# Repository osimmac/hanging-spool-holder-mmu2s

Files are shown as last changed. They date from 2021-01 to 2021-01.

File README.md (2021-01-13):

# hanging-spool-holder-mmu2s
OpenSCAD design of a hanging spool holder, designed with simplicity, low friction, and reusing parts from MMU2S kit in mind.

--Features
 - Minimalist strong design, no supports needed, simple geometry
 - Reuses MMU2S Spool holder hardware, create up to 10 hanging spool holders!
 - High tech Self Stablizing roller, see this video for an explanation of how it works! (it was also the inspiration for the roller design) https://www.youtube.com/watch?v=Ku8BOBwD4hc
 - low rolling resistance, perfect for flexible filaments in the MMU2S! (ive had success printing 85A hardness filaments!)

--Required Hardware
- 1x Rod that came with MMU2S trays
- 2x Bearings that came with MMU2S trays 
- 2-4x Zipties that came with printer or MMU2S
- 0.8mm nozzle recommended

--How to get started if new to OpenSCAD
1. Download and install from here (os specific instructions are there): https://www.openscad.org/downloads.html
2. launch openscad and start messing around with the examples, they can be accessed from the launcher or "file" at the top of the application.  most of what i learned is from there. the examples are easy to modify and expand upon.
3. Check out the Basics > CSG-Modules.scad example, this spool holder uses modules. (though it could use them better)
3. Useful cheatsheet once you understand how the commands work: https://www.openscad.org/cheatsheet/index.html

--How to get started if not new to OpenSCAD :)
1. download and open spoolholder.scad from this repository
2. there are many comments within the file that explain whats going on; generally you will need to edit the variables near the top
3. comment out a few lines in the RENDERING /OUTPUT section, start with leaving test piece uncommented if you need to adjust fitment
4. Render (F6)
5. if it looks good, Export to STL (F7)!

--How to Print
(print test piece first)

Highly Recommend nozzle larger than 0.4mm, especially if using MMU2S. Less layer changes, less filiament swaps, smaller purge blocks with thicker layer heights, Faster Prints. they are cheap and worth it. This spool holder can be printed in under 3 hours while still making a strong print. I dont have settings for anything other than 0.8mm, you are welcome to try and post results as an issue or something.

(*used prusa slicer*)
  
  - PETG filament thats strong and reliable (you dont want 1kg mass falling on your printer)
  - Bed temp 70c, add gluestick, first layer temp 255c, other layers 265c
  - I had my petg set to 12mm^3/s max volumetric speed, its near the limit but allows for fast strong prints. its also why temp is so high.
  - I used a 0.6mm profile as a starting point and scaled all the settings for 0.8mm nozzle.
  - 0.8mm nozzle, recommend tuning extrusion multiplier, mine is set to 1.08
  - retraction for 0.8mm nozzle was set to 0.4mm
  - Extrusion width for 1st layer is 150%
  - all other extrusion width settings set to 0.9mm
  - 0.6mm layer height
  - 3 perimeters
  - 2 top and bottom layers
  - Rectiliear infill, 10% density on the interior
  - fast print speed settings, first layer speed set to 10mm/s
  - no support
  - make sure first layer sticks well
  - min 30% fan max 70%, disabled for first 2 layers, slow down if print speed is below 8 seconds per layer
        -slow down at most 4mm/s for cooling

--How to assemble
1. First print test piece with settings above
2. Clean out the hole with a razer or something, be careful not to enlarge the hole too much or break the blade. 
3. Get a rod and try push fitting it into the hole, it will require a lot of force
4. Try using a hammer, with plastic part facing down and rod pushing into carpet or something. dont bang the rod and dont do it on tile as the force may break it. gently but firmly hammer the test piece onto the rob. it should go in about 1cm. a full inserted rod will stick out about 10.8cm from the piece. its OK if a bit more sticks out if it feels secured. ideally 9mm or more will enter the part.. 
5. If it doesnt fit properly, try altering the test piece with openscad and generate an updated STL.
6. Repeat steps above until you get a good fitting rod that can hold 1kg without bending a bunch. 
7. Generate a new main arm if you altered the hole size.
8. Print everything
9. Trim parts
10. Press fit bearings into roller, be careful not to break it
11. Press fit rod into main arm, use hammer on plasic piece with rod in carpet.
12. Slide roller on, verify it rolls smoothly
13. press fit cap on, may need to trim peg
14. hang with zipties!

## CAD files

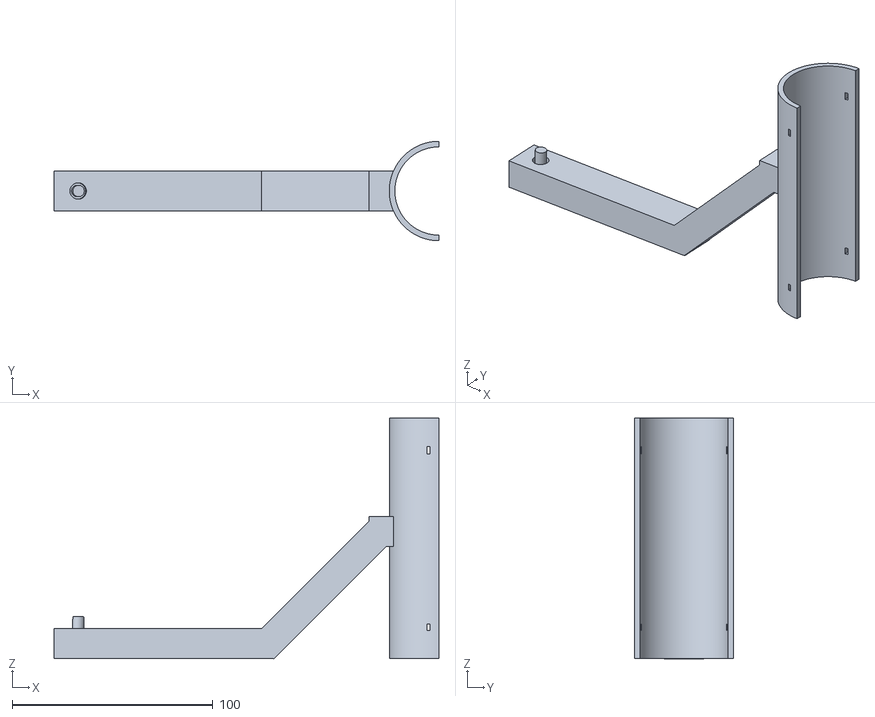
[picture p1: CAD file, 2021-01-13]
spoolholderfinal.stl
192.0 x 49.6 x 120.1

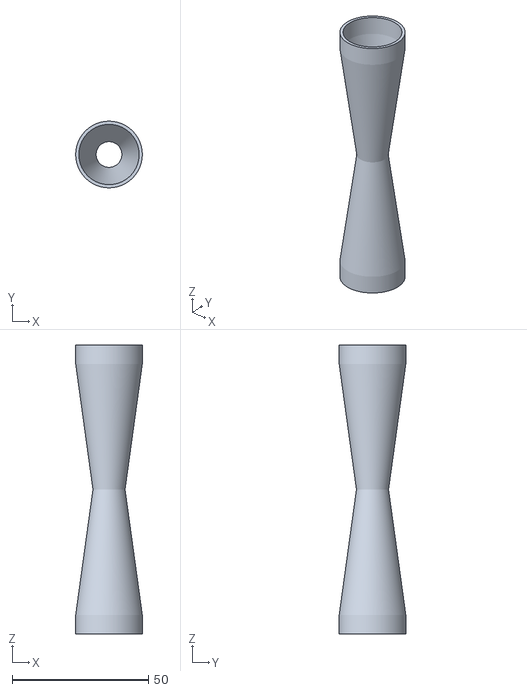
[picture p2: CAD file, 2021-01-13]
spoolrollerfinal.stl
24.4 x 24.4 x 106.0

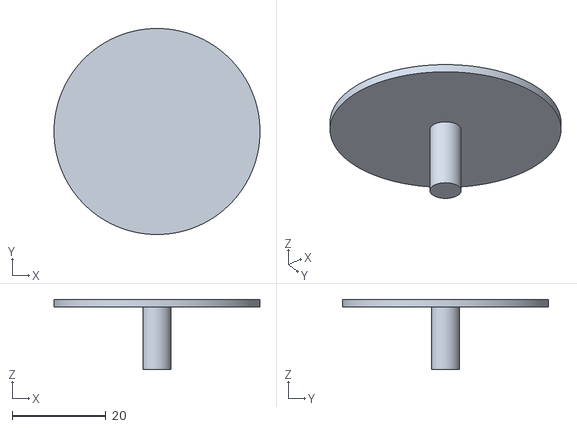
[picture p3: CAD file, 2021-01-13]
spoolcap.stl
44.0 x 44.0 x 15.0

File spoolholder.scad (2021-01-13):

  //  This program is free software: you can redistribute it and/or modify
  //  it under the terms of the GNU General Public License as published by
 ///   the Free Software Foundation, either version 3 of the License, or
 //   (at your option) any later version.
//
 //   This program is distributed in the hope that it will be useful,
  //  but WITHOUT ANY WARRANTY; without even the implied warranty of
  //  MERCHANTABILITY or FITNESS FOR A PARTICULAR PURPOSE.  See the
 //   GNU General Public License for more details.

 //   You should have received a copy of the GNU General Public License
 //   along with this program.  If not, see <https://www.gnu.org/licenses/>.

//FILAMENT SPOOL HOLDER DESIGNED FOR USE WITH MMU2S HARDWARE
//Designed by osimmac


//Dont mess with these variables
// Global resolution
$fs = 0.01;  // Don't generate smaller facets than 0.01 mm
$fa = 1;    // Don't generate larger angles than 5 degrees



//CONSTANTS FOR REFERENCE!
//bearing diameter = 22mm
//rod diameter = 7.85mm
//rod hole diameter = 6mm


//User Variables
//MAIN ARM VARIABLES
//Rod Hole size
  //changing the value below will change the size of the hole the rod is inserted to. try changing the size in 0.05 or 0.1mm increments. 
 holediameter = 8.2;
 
 //Rod peg size
  //changes size of peg that goes into rod
  pegdiameter = 5.7;
  
  
  //ROLLER VARIABLES
 //changes hole diameter for bearing
bearingdiameter = 22.08;


  //CAP VARIABLES
   //changes size of peg that goes into other end of rod, should be more snug than rodpegsize
  cappegdiameter = 5.75;


//RENDERING / OUTPUT BEGIN
//Leave only 1 uncommented to render and get STL for that object only. alter and print just the test piece if you need to adjust fitment for rod. If you just edit the fitment for the hole, then you can use orignal cap and roller stl and just render a new Main Arm. if not, do this  for each of the 3 pieces. spollroller(); should stay commented as its depricated.
//spoolroller();

//Test  Piece!!
translate([-50,0,0])testpiece();

//Roller Piece
 spoolroller2();
 
 //Cap Piece
rotate(180,[0,1,0])translate([0,0,-108])spoolcap();
 //Main Arm Piece
translate([0,0,-2])spoolarm();

//once setup, press f6 to render and then f7 to export as stl. these actions are also at the top of application. may need to add .stl to end of file when exporting.

//RENDERING /OUTPUT END!!!




//BEGINNGING OF ACTUAL CODE
//This spool holder is spilt up into modules/parts, these parts are:
//---Test Piece (for testing fitment)
//---Spool Roller 2 (it has the angled center)
//---Spool Rolled (depricated and lame)
//---Spool Cap (cap on the end)
//---Spool Arm (main structure)

//Test piece to test fitment of rod.
//Should be hard to insert but not impossible, it should go in around 1cm and feel secure
//NOTE: there is a 1.7 degree tilt in the hole to counter act sag when loaded with filament
module testpiece(){

    union(){
       
    rotate(1.7,[0,1,0])translate([0,0,-13])color("DarkGreen")cylinder(h=20,r=pegdiameter/2);
    difference(){
    translate([-12,-10,-14])color("Green")cube([25,20,15]);
     //changing the radius (r) of the cyclinder below will change the size of the hole the rod is inserted to. try changing the size in .05 or .1mm increments. 
    rotate(1.7,[0,1,0])translate([0,0,-11.8])cylinder(h=13,r=holediameter/2);
    }
    }

  
   }

//high tech self stablizing roller 
 //this is created by making a long thin polygon with 3 bends in it, requiring 10 points, translating it away from the origin by the radius of bearing and rotate extruding it around the z axis.
   
   //polygons start at the origin and work their way from there. its basically 2 lines with 5 points, offset with thickness of walls desired.
module spoolroller2(){

     color("Purple")rotate_extrude(angle=360) {
         translate([bearingdiameter/2,0,0])rotate([0,0,0])polygon([[0,0],[0,7.05],[-6.325,106/2],[0,106-7.05],[0,106],[1.175,106],[1.175,106-7.05],[-5.15,106/2],[1.175,7.05],[1.175,0]]);
     }
}

//deprecated flat roller
module spoolroller(){
    difference(){
    color("Blue")cylinder(h=106,r=bearingdiameter+2.4/2);
    translate([0,0,-.05])color("Red")
                            cylinder (h=106.1,r = bearingdiameter/2);
}
}   


//cap that goes on other end of rod and acts as safeguard preventing spool from coming off
module spoolcap(){
    union(){
    color("Cyan")cylinder(h=15,r=cappegdiameter/2);
    color("LightBlue")cylinder(h=1.6,r=22.05);
    }
}


//This is the main arm that the
//rod is pushed into
module spoolarm(){
    union(){
    union(){
 //union for angled cube and cube with hole
    union(){
 //union for peg and cube with hole
    union(){
 
        
   
    rotate(2,[0,1,0])translate([0,0,-13])color("DarkGreen")cylinder(h=20,r=pegdiameter/2);
   //difference to make cube with hole
    difference(){
   //cube that rod inserts to and extends it the x direction
    translate([-12,-10,-14])color("Green")cube([110,20,15]);
    //hole for rod
    rotate(2,[0,1,0])translate([0,0,-11.8])cylinder(h=13,r=holediameter/2);
    }
    }
    
   //angled cube 
  rotate(315,[0,1,0])translate([59,-10,-79])cube([85,20,15]);
    
    }


//EVERYTHING BELOW THIS COMMENT IS RELATED TO THE HALFPIPE/ PART SECURING THE ARM!
    //difference for zip tie holes
    difference(){
     
     //difference for cube that cuts pipe into halfpipe
    difference(){
       //difference that creates hollow tube / pipe
    difference(){
   translate([180,0,-14])cylinder(h=120, r= 24.8);
    translate([180,0,-14.01])cylinder(h=121, r= 22);
    } 
    //cube that cuts pipe in half
    translate([180,-30,-20])cube([200,200,200]);
}   
    //union for ziptie holes to be 1 object for difference
    union(){
    //Holes for Zipties
    //Change translate of both below to move them around
    translate([174,-50,0])cube([1.6,100,3.4]);
    translate([174,-50,88])cube([1.6,109,3.8]);
    }
}
    //cubes that connects halfpipe to rest of arm, the first one if for a bit of extra support
    rotate(0,[0,1,0])translate([145,-10,42])cube([5,20,15]);
}
translate([147,-10,42])cube([11,20,15]);
}
}
